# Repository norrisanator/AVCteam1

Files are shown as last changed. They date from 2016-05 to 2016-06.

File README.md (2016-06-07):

# AVCteam Numoro Uno
AVC stuff. 
##Checklist for Week One
- [x] Hardware: Plan the robot, and create a prototype of how the robot will work most efficently
- [ ] Software: Working out what the values the sensor are going to give
- [x] Software: How to send code to the pi
- [x] Software: Constructing code for the robot to go forwards
- [x] Simran: Write a progress report for week one

##Week One Review
- We planned the robot, and we were able to make a prototype of the robot and see if it was efficent enough *(this is a base for the robot so that it is in a functional state to test code with)*.
- Since we did not get how to work out what the sensor values are going to give, the software team will try completing this      task next week.
- We connected up the pi, and were able to send code to it
- Everyone has signed the AVC plan and submitted it.
- We all attended the labs/meetings held

##Checklist for Week Two
- [x] Hardware: Choose the design for the robot
- [x] Software: Fix the bug (get_pixel() returning a row out of range error, *row and col values needed to be swapped*)
- [x] Software: Working out what the values the sensor are going to give
- [ ] Software: Try get the robot to follow the line for quadrant one
- [x] Simran: Write a progress report for week two
- [x] Simran: Plan a structure for the progress report

##Week Two Review
- The hardware have decided on the design/theme of the robot *(focus on being short in length for maze corners)*
    Side affect of short design is robot is tall making it unstable in abrupt turns, due to this may change to small wheels to reduce height
- We were able to fix the bug we encountered in the lab by swapping row and col values in the get_Pixel()
- We were not able to get the robot to follow the line for quadrant one (the robot kept spinning in a circle, this is happened   because we had an error in the code), we will complete this in week three.
- Everyone attended the lab this week

##Checklist for Week Three
- [x] Hardware: Making something to support the IR sensors 
- [x] Hardware: Change the position of the camera
- [x] Hardware: Change the wheels to smaller 
- [x] Software: Fix error in the code to make the robot follow the line for quadrant one
- [x] Simran: Weekly Report
- [x] All: Discuss the progress report, so we all write similar things
- [x] Software: Sending code to sever to open gate

##Week Three Review
- Everyone attended the Lab session
- We decided to record the testing we are doing in this weeks reviews, as our understanding and code is at a stage where the robot will begin to function as intened. This also allows the team to access it and use it in their report.
- Hardware: We are putting the camera on an angle again so we can see the line and what is on either side of it, this is to solve an issue of having the camera facing straigth down and located low resulting in it being able to see a very little area including the line but not much either side making controlling movement difficult/impossible.
- Software (Testing): More code fixing and adapting through tests. Testing showed us that the robot was moving to fast as it kept losing the line. We also found that that it could cope with one side of the white line and not the other. This was because it is over adjusting too much.
-Software (Testing): We fixed the robot spinning in circles by making one of the motor speeds negative because before we had both motor speeds at positive *issue arose while making code changes*. Making one negative and the other positive makes the wheels both turn the same way.
- Software (Testing): We also had an error that the robot was adjusting to the wrong side of the line *turning the opposite way to that expected*, we fixed this by changing the value of the proportional value (from negative to positive and positive to negative) *Wheels had been turning the wrong way*
- Software (testing): Halved the kp (proportional constant) constant which made the robot follow the line much better.
- We fixed the noticed errors and managed to get the robot through quadrant one
- Software: Gate sucessfully opened. Need to implement code to make it wait at gate for it to open
- Since we did not didnt make something to support the IR sensors we will do that next week

##Checklist for Week Four
- [ ] Software: Tune line following code. Make it more smoother
- [ ] Software: Handle junctions on line.
- [x] Hardware: Plan mount for IR sensors
- [x] Software: Get sensor value from IR sensors
- [x] Hardware: Finalise plan for robot's look
- [x] Simran: write progress report for week four

##Week Four Review
- Everyone attended the lab
- We will try completing the software tasks next week
- Worked on 3D printing, and now ready to print
- Got most of 3D printing done

##Checklist for Week Five
- [x] get 3D printing done
- [ ] Software: Tune line following code. Make it more smoother
- [ ] Software: Handle junctions on line.
- [ ] Simran: Write progress report 

##Week Five Review
- Everyone attended the lab
- Hardware: We decided to move the camera further back from its positions because the software team picked up we were seeing     the line to far out which effected the turning of the robot, as it turned too soon
- Hardware: Didnt get the 3D printing done in lab because the 3D printers broke, but we wil get them done this week

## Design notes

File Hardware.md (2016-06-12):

#Hardware Information Log

###Part Sizes:
|Part | Length *(mm)*| Width *(mm)*| Heigth *(mm)*|
|---| ---| ---| ---|
|Power Board |118 |64 |
|RPi |85 |56 |17 |
|Camera |25 |25 |
|I.R |20 |45 |
|**Wheel Size** | **Diameter _(mm)_**  |
|Small |30 |
|Medium |60 |
|Large |90 |

#####Week 1. Plan 
The plan for hardware is get the bot to be set up to be functional to be able to access all ports without having to remove parts. Also to be small enough to be able to move through the maze with ease. 

#####Week 2. Decisions 
We have assembled the bot in to a basic small frame that fits everything above the two motor wheels, with a free moving back wheel. The power board and raspberry pi are mounted above one another in a two tier layout. We believe this to best functional layout with access to all inputs, as well as space for the battery. The Camera is mounted to the chassis with a two hinge arm that holds it out at any required angle. We have used the medium size wheels (60mm) which we believe to be the best size for the bot.

#####Week 3. Testing
While testing the bot we discovered that the bot was a little unstable, the battery was not holding its place and the camera mount was moving around. This caused us to switch down to the smaller wheels bringing the centre of gravity down. We took the arm off the camera mount and then creating a new mount with the parts from the old one. Then attaching the camera directly to the chassis point directly towards the ground to read the line. Using one of the hinges from the camera mount and some other supports we managed to get a battery support/brace. 

#####Week 4. First quadrant. 
First time using the alterations from week 3, we found out that the camera needed to be on a slight angle or elevated higher *(was unable to see the line and enough area on both sides)*. Using parts that we had we got the camera on to a single hinge mount and got it into a stable position. The bot successfully went through the first quadrant! 
We are now looking at getting mounts for the three I.R sensors that will get the bot through the maze. 

######I.R Sensor Placement
* Two sensors will be angled with brackets either attached to the supports for the board or built into the supports for the board
* A third will be mounted facing forward on the front centre
  * This creates slight issues with the camera mount, *current thought is to put a bracket bellow the camera*
 
######Other Possible 3D Printing _not yet required_
- [x] Block for motor mount to make the robot flat
- [x] Bracket to raise camera height that is fixed *(not hinged)*

*In the end all parts being 3D printed. This included the braces for the Rpi and power board to be mounted on. The front braces also had mounts for two of the angeled front I.R sensors. Also printed off a Camera holder with a I.R front mount below it facing forward. We ended up also printing out a base cassis that had the correct thinkness for the motors to be mounted flat. As well as space for the wires to be hidden. 
###3D printed Part Sizes:
|Part        | Width *(mm)*| Height *(mm)*| Length*(mm)*
|------------| ------------| -------------| -------------|  *IR mounts attached to the front bracing and Camera mount. 
|Bracing     |2            |70            |10
|Base        |55           |10            |135
|I.R mount*  |2            |50            |10
|Camera Mount|25           |2             |32

!! Also see photo with visual measurements. 
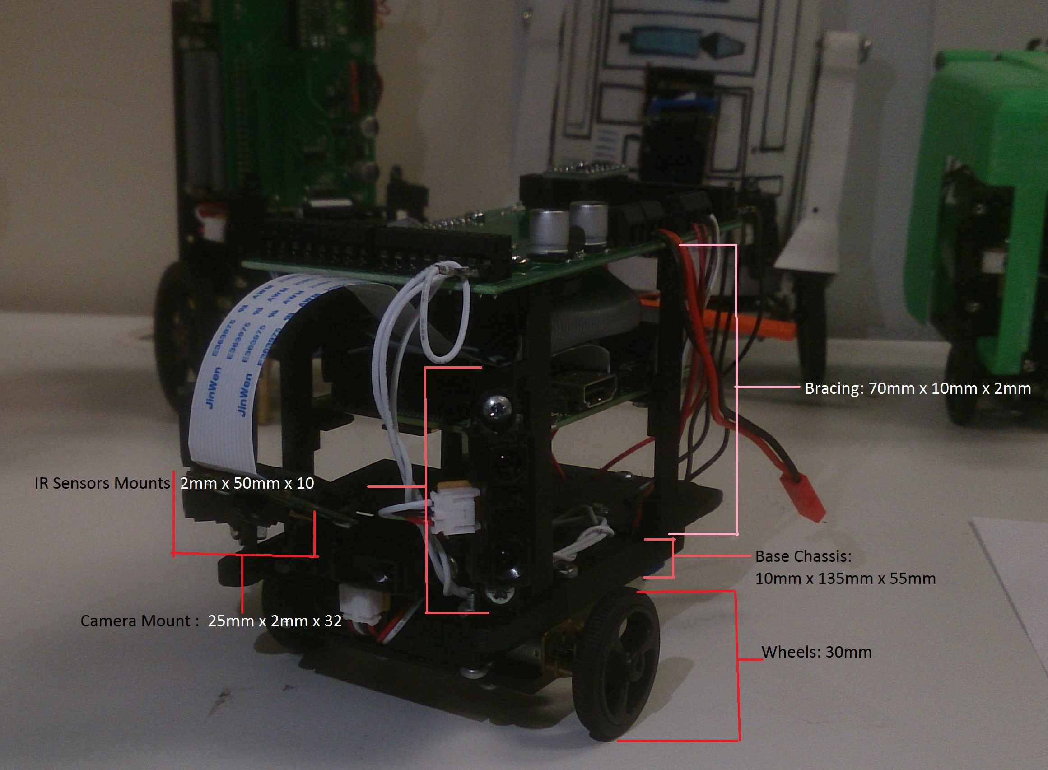
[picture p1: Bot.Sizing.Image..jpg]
Visual Measurements


All Parts attached using a mix of 2mm screws and nuts varing in length from 4mm - 16mm. (maybe some hot glue aswell)  
- Motors and bracing attached to the Chassis using 2mm by 16mm screw and nut. 
- Raspberry Pi, Camera and IR sensors attached to bracing using 2mm by 4mm screw. 
- Power board and Camera mount attached to bracing uing 2mm by 8mm screw and nut.
- There were two pieces of plastic hot glued to the bottom to hold wires in place.

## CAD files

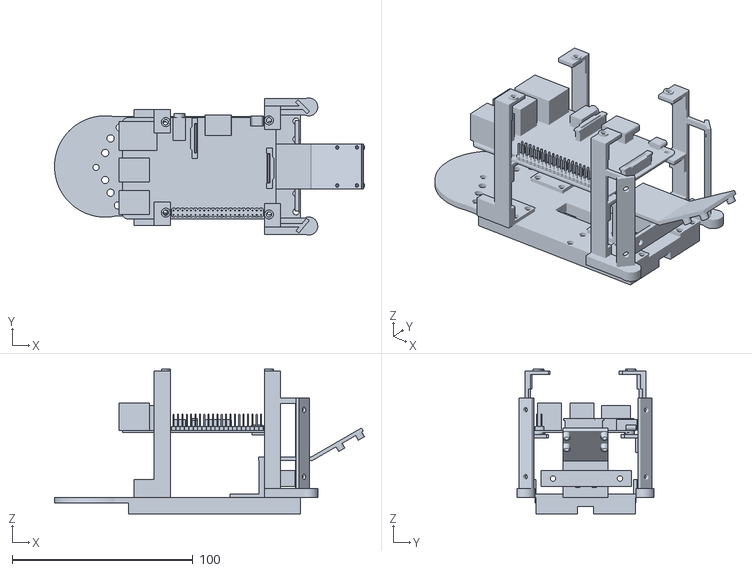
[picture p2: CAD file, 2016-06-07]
3D.Printed parts.with.pi..stl
171.3 x 75.8 x 80.0

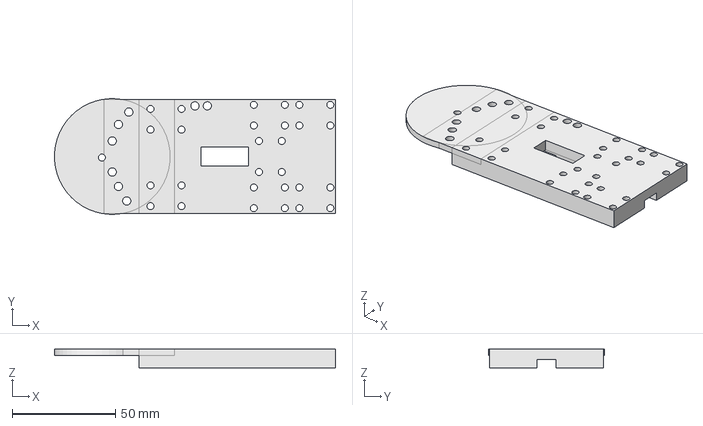
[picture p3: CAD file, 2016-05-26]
Final.Design.including.base.FCStd
135.9 x 55.9 x 9.00 mm

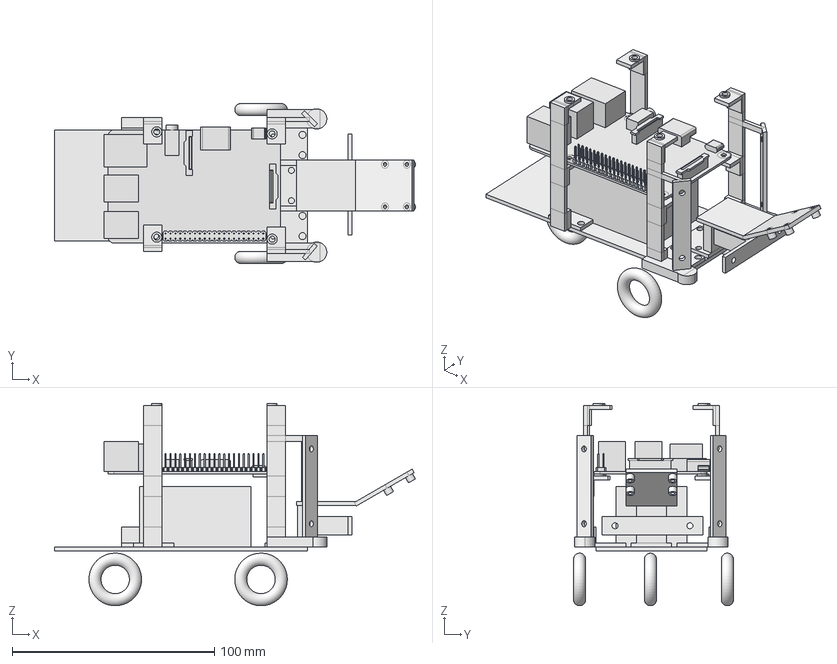
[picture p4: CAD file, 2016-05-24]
TEST.SIZING.NO.2.FCStd
178.3 x 79.0 x 100.0 mm
Base.Cassis
RASPBERRY PI 3

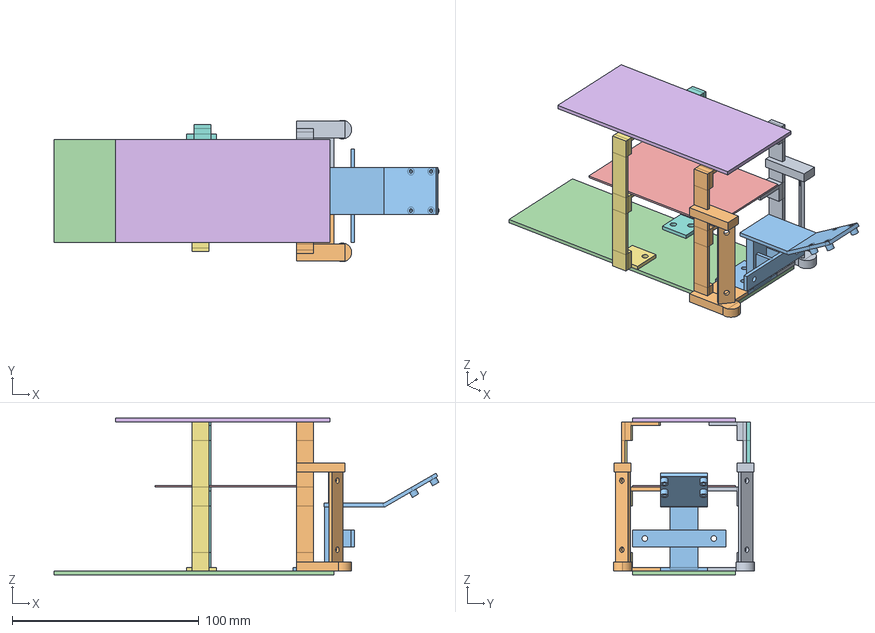
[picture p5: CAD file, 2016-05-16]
TEST.SIZING..FCStd
206.3 x 75.8 x 84.0 mm
Front.left.Brace
Front.right.Brace
Camera.Mount
Base.Cassis
R.PI
Power.Board

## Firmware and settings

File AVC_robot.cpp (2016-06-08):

#include  <stdio.h>
#include  <time.h>
#include <csignal>
#include <cstdlib>
// constants
#define MESSAGE_LENGTH 6
#define MOTOR_SPEED 50
#define SLEEP_TIME 100000
#define PICTURE_WIDTH 320
#define PICTURE_HEIGHT 240
#define THRESHOLD 500000
//proportional constant
#define KP 0.0015
//derivative constant
#define KD 0.0005
//integral constant
#define KI 0
#define MAZE_KP 0.05
#define MAZE_KD 0
#define MAZE_KI 0
//line following methods
extern "C" int init(int d_lev);
extern "C" int take_picture();
extern "C" char get_pixel(int row,int col,int colour);
extern "C" int Sleep( int sec, int usec );
// Motor is the pin it is connected to, dir is direction 1 or 2, speed is 0-255
extern "C" int set_motor(int motor, int speed);
//Server methods
extern "C" int connect_to_server( char server_addr[15],int port);
extern "C" int send_to_server(char message[24]);
extern "C" int receive_from_server(char message[24]);
//Digital sensors methods
extern "C" int init(int d_lev);
extern "C" int read_analog(int ch_adc);
//extern "C" int select_IO(int chan, int direct);

void maze();
//stops motors spinning
void handle_signal(int signal){
    if(signal == SIGINT){
        set_motor(1, 0);
        set_motor(2, 0);
        
        std::exit(0);
    }
}
// https://github.com/kaiwhata/ENGR101-2016/wiki/Network-commands
// more detail on open gate
void openGate(){
    connect_to_server((char *)"130.195.6.196", 1024);
    send_to_server((char *)"Please");
    char message[24];
    receive_from_server(message);
    // null character limits message length at 6 characters long
    message[MESSAGE_LENGTH] = '\0';
    send_to_server(message);
    printf("%s", message);
}

void testSensors(){
    //int select_IO(0, 1);
    int analog_sensor_reading = read_analog(0);
    printf("%d\n",analog_sensor_reading);
    Sleep(0,500000);
}


int main(){
    // Sets up raspbery pi hardware and ensures everything is working.
    init(0);
    
    std::signal(SIGINT, handle_signal);
    
    openGate();
    
    // Test code for camera, takes picture and prints it.
    int black_count = 0;
    int counter = 0;
    bool first_full_line = true;
    //maze();
    while(true){
        // Reads current image from camera stores in memory.
        take_picture();
        int total=0;
        int total_error = 0;
        int num_white = 0;
        int num_col_white = 0;
        int total_white = 0;
        int prev_error = 0;
        bool c;
        // loop takes a line of pixels 5 wide horizontally accross the picture
        for(int i=0; i<PICTURE_WIDTH; i++){
            for(int j = 0; j<5; j++){
                // c gets assigned 0 or 1
                c = get_pixel(i, (PICTURE_HEIGHT/2)+j, 3) > 127;
                // 0 or 1 added to total_white
                total_white += c;
            }
            // num_white gets the values from just 1 pixel line across the picture.
            c = get_pixel(i, PICTURE_HEIGHT/2, 3) > 127;
            num_white += c;
            // added to the total
            total += (i-(PICTURE_WIDTH/2))*c;
        }
        
        total_error += total;
        // PID control see https://github.com/kaiwhata/ENGR101-2016/wiki/PID-(Proportional-Integral-Derivative)-Control
        // for more detail
        double proportional_signal = total*KP;
        double derivative_signal = (total-prev_error/0.1)*KD;
        double integral_signal =  total_error*KI;
        prev_error = total;
        int total_signal = proportional_signal + derivative_signal + integral_signal;
        //deadend checker
        counter++;
        // if the camera sees nothing but black implements black_count
        if(num_white == 0){
            black_count++;
        }
        // takes a picture of a verticle column in centre of picture
        // currently unused.
        for(int i=0; i<PICTURE_HEIGHT; i++){
            c = get_pixel(PICTURE_WIDTH/2, i, 3) > 127;
            num_col_white += c;
        }
        // detecting if picture is fully white, e.g. only see white
        if (num_white >= 320){
            printf("hit\n");
            if(first_full_line == true){
                // drives straight through
                first_full_line = false;
                set_motor(1, MOTOR_SPEED);
                set_motor(2, -MOTOR_SPEED);
                Sleep(1,0);
            } else {
                //turns left
                set_motor(1, -MOTOR_SPEED - total_signal);
                set_motor(2, -MOTOR_SPEED - total_signal);
            }
        } else if(num_white > 0){
            // drives forward
            set_motor(1, MOTOR_SPEED - total_signal);
            set_motor(2, -MOTOR_SPEED - total_signal);
        } else {
            // turns
            set_motor(1, -MOTOR_SPEED);
            set_motor(2, MOTOR_SPEED);
        }
        // if stuck at dead end for too long spins around
        if(black_count == 25){
            black_count = 0;
            set_motor(1, MOTOR_SPEED);
            //turns avc around
            set_motor(2, MOTOR_SPEED);
            Sleep(1,0);
        }
        //resetes counting how many times it detects dead end.
        if(counter == 60){
            counter = 0;
            black_count =0;
        }

        /*printf("num white:%d\n", num_white);
        printf("black:%d\n", black_count);
        printf("Counter:%d\n", counter);
        printf("Row:%d\n", num_white);
        printf("Col:%d\n", num_col_white);*/
        
        // detecting if at red square for start of maze    
        int num_red = 0;
        for(int i=0; i<PICTURE_WIDTH; i++){
            bool r = get_pixel(i, PICTURE_WIDTH/2, 0) > 200;
            bool g = get_pixel(i, PICTURE_WIDTH/2, 1) > 200;
            bool b = get_pixel(i, PICTURE_WIDTH/2, 2) > 200;
            if(r && !g && !b){
                num_red++;
            }
        }
        //printf("Red:%d\n", num_red);
        if(num_red > 100){
            set_motor(1, 0);
            set_motor(2, 0);
            maze();
        }
           
        Sleep(0,SLEEP_TIME);
    }
    return 0;
}
void maze(){
    // maze code
    int prev_error = 0;
    int total_error = 0;
    while(true){
        int ir_sensor_left = read_analog(2);
        int ir_sensor_right = read_analog(1);
        int ir_sensor_forward = read_analog(0);
        printf("Left:%d\n", ir_sensor_left);
        printf("Right:%d\n", ir_sensor_right);
        printf("Ford:%d\n", ir_sensor_forward);
        int error_signal = ir_sensor_right - ir_sensor_left;
        total_error += error_signal;
        // see PID control https://github.com/kaiwhata/ENGR101-2016/wiki/PID-(Proportional-Integral-Derivative)-Control
        double proportional_signal = error_signal*MAZE_KP;
        double derivative_signal = (error_signal-prev_error/0.1)*MAZE_KD;
        double integral_signal =  total_error*MAZE_KI;
        prev_error = error_signal;

        int total_signal = proportional_signal + derivative_signal + integral_signal;
        // robot will always turn right
        if(ir_sensor_right < 130){
            printf("hi\n");
            set_motor(1, MOTOR_SPEED);
            set_motor(2, -MOTOR_SPEED);
            Sleep(0, 800000);
            set_motor(1, MOTOR_SPEED);
            set_motor(2, 0);
            Sleep(1,500000);
            ir_sensor_right = read_analog(2);
            /*if(ir_sensor_right < 130){
                set_motor(1, MOTOR_SPEED);
                set_motor(2, -MOTOR_SPEED);
                Sleep(0, 500000);
                set_motor(1, MOTOR_SPEED);
                set_motor(2, 0);
                Sleep(1,0);
            }*/
        } else if(ir_sensor_forward > 300){
            // spins robot around
            set_motor(1, -MOTOR_SPEED);
            set_motor(2, -MOTOR_SPEED);
        } else {
            // goes straight forward
            set_motor(1, MOTOR_SPEED - total_signal);
            set_motor(2, -MOTOR_SPEED - total_signal);
        }
        
        Sleep(0,SLEEP_TIME);
    }
    return;
}

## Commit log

2016-04-21 Update AVC_robot.c
    Set up some example code for taking picture and getting the "whiteness" of each pixel.
    Prints every half a second
2016-04-21 Fix code and add motor test
    [AVC_robot.cpp]
2016-04-21 Change camera reading to get pixels from whole row
2016-05-05 Network code.
    Sends message to server.
    Gets message back from server and prints it.
2016-05-11 PID improvment
2016-05-11 Replace tabs with spaces
    [AVC_robot.cpp]
2016-05-12 More PID improvements
2016-05-12 Formatting and more current status detail
    Made some formatting to make the Hardware log easier to read.
    Changed measurements to mm as most 3D model programs use mm
    Also added some more information to the current status and work needing to be done.
2016-05-16 Testing sizes.
    I have combined all the separate parts that I would like to print.
    I had added in the R-pi, power board thing and chassis to be able to visualize it together.. the parts that I am wanting to print are the two front braces that have the IR mounts on them (the IR moun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
    Have a look and let me know what you think could do with improving.
    Have based this on what we discussed during the LABS.
    Alex.
    [TEST.SIZING..FCStd]
2016-05-18 Added code for testing digital sensors.
2016-05-18 testing digital sensor
2016-05-18 Added motor speed variable
2016-05-19 added more to psuedo and fixed dead end line code(probably)
    [AVC_robot.cpp]
2016-05-19 updtated pid values
2016-05-22 print value of num_white
2016-05-24 The lay out of what is going to be printed.
    this is the final layout for the bot.. It is what will / has been printed.
    [TEST.SIZING.NO.2.FCStd]
2016-05-24 changed motor direction
2016-05-25 printing c a
2016-05-25 testing camera values
2016-05-26 Fixed prev error initializing to 0 each loop
    [AVC_01.cpp]
2016-05-26 Final design.
    this is the actual final design now that includes a printable chassis. With Cuts/holes to be able to attach motors and the frame. including cut out for wires.
    [Final.Design.including.base.FCStd]
2016-05-26 checking sensors connections
2016-05-26 Corrected ananlog variables to right sensors
    [AVC_robot.cpp]
2016-05-27 Added test sensor program
2016-06-07 Updating what we printed.
2016-06-07 All parts that were printed for the final design.
    Have uploaded in STL format as i believe you should be able to view with out opening it in CAD.
    [3D.Printed parts.with.pi..stl]
2016-06-08 Added comments explaining code.
    Code for turning on line may not be 100% accurate but shouldn't matter too much
    [AVC_robot.cpp]
2016-06-08 Updating hardware.
    Made table for printed parts + how parts were attached to one another.
2016-06-08 Shows the Sizing Visually on photo.
    Just to make it visually clear what the size of each part that was printed.
2016-06-12 Fixed a couple of measurement mistakes
